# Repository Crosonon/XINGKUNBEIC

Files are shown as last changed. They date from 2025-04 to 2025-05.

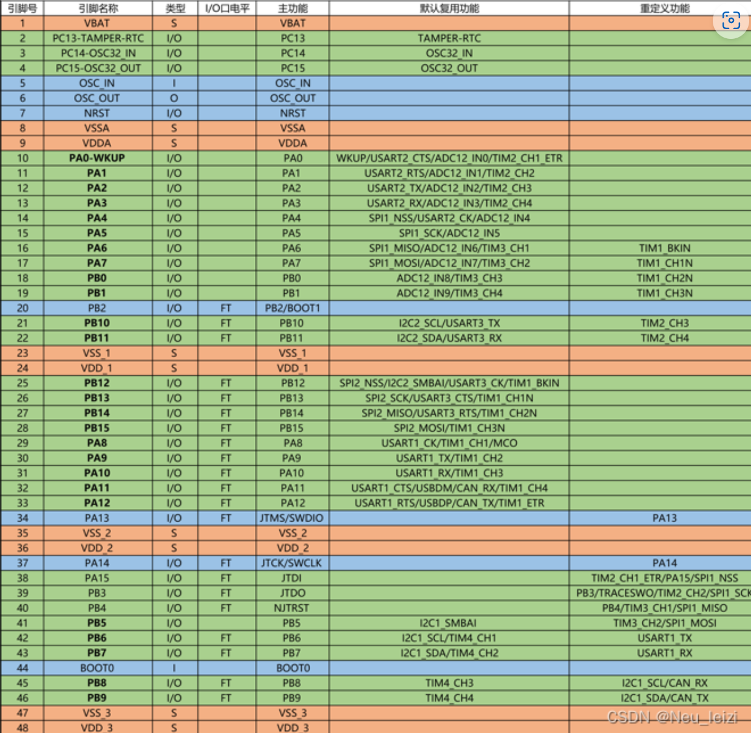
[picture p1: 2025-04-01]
Hardware/32引脚.png

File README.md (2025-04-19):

这是易柏队2025星坤杯C题的仓库！

## 题目要求
一、 任务 
设计制作一个运动目标控制与自动追踪系统。系统包括模拟目标运动的红色光斑位置
控制系统和指示自动追踪的绿色光斑位置控制系统。系统结构示意及摆放位置见图 1
（a）。图中两个激光笔固定在各自独立的二维电控云台上。 

 红色激光笔发射的光斑用来模拟运动目标，光斑落在正前方距离 1m 处的白色屏幕上，
光斑直径≤1cm。红色光斑位置控制系统控制光斑能在屏幕范围内任意移动。绿色激光笔发
射的光斑由绿色光斑位置系统控制，用于自动追踪屏幕上的红色光斑，指示目标的自动追踪
效果，光斑直径≤1cm。绿色激光笔放置线段如 图 1（b）所示，该线段与屏幕平行，位于
红色激光笔两侧，距红色激光笔距离大 
于 0.4m、小于 1m。绿色激光笔在两个放置线段上任意放置。屏幕为白色，有效面积大于 
0.6╳0.6m2。用铅笔在屏幕中心画出一个边长 0.5m 的正方形，标识屏幕的边线；所画的正
方形的中心为原点，用铅笔画出原点位置，所用铅笔痕迹宽≤1mm。 
二、 要求 
1. 基本要求 
（1）设置运动目标位置复位功能。执行此功能，红色光斑能从屏幕任意位置回到原点。光
斑中心距原点误差≤2cm。 
（2）启动运动目标控制系统。红色光斑能在 30 秒内沿屏幕四周边线顺时针移动一周，移
动时光斑中心距边线距离≤2cm。 
（3）用约 1.8cm 宽的黑色电工胶带沿 A4 纸四边贴一个长方形，构成 A4 靶纸。将此 A4 
靶纸贴在屏幕自定的位置。启动运动目标控制系统，红色光斑能在 30 秒内沿胶带顺时针移
动一周。超时不得分，光斑完全脱离胶带一次扣 2 分，连续脱离胶带移动 5cm 以上记为 0 
分。 
（4）将上述 A4 靶纸以任意旋转角度贴在屏幕任意位置。启动运动目标控制系统，要求同
（3）。 
2. 发挥部分 
（1）运动目标位置复位，一键启动自动追踪系统，控制绿色光斑能在 2 秒内追踪红色光
斑，追踪成功发出连续声光提示。此时两个光斑中心距离应≤3cm。 
（2）运动目标重复基本要求（3）~（4）的动作。绿色激光笔发射端可以放置在其放置线段的任意位置，同时启动运动目标及自动追踪系统，绿色光斑能自动追踪红色光斑。启动系统 
2 秒后，应追踪成功，发出连续声光提示。此后，追踪过程中两个光斑中心距离大于 3cm 
时，定义为追踪失败，一次扣 2 分。连续追踪失败 3 秒以上记为 0 分。运动目标控制系
统和自动追踪系统均需设置暂停键。同时按下暂停键，红色和绿色光斑应立即制动，以便测
量两个光斑中心距离。 
（3）其他。 
三、 说明 
（1）红色、绿色光斑位置控制系统必须相互独立，之间不得有任何方式通信；光斑直径小
于 1cm；屏幕上无任何电子元件；控制系统不能采用台式计算机或笔记本电脑。不符合要求
不进行测试。 
（2）基本要求（3）、（4）未得分不进行发挥部分（2）的测试。 

## 引脚分配

**以下必要**

1. 步进电机 gpio*6
2. k210 uart*1
3. 激光笔 GPIO*1
4. 按键 GPIO*5
5. led GPIO*2
6. oled 硬件iic*1

**以下非必要**

1. 蓝牙 uart*1
2. 超声波 GPIO*2

| 模块 | 引脚 | 用途（外设） | 模块 | 引脚 |
| --- | --- | --- | --- | --- |
| 步进电机 | a8 | step | 激光笔 | b3 |
| 步进电机 | b4(原a9) | step | 按键 | b8 b9 a10 a11 a12 |
| 步进电机 | b12 b13  | en | led | a6 a7 |
| 步进电机 | b14 b15  | dir | 蜂鸣器 | a9(原b4) |
| K210 | a3 | rx2（接k210的tx） | 超声波 | a9 |
| K210 | a2 | tx | | a5 |
| OLED | b10 | scl | 预留蓝牙 | b7  rx1（接蓝牙tx） |
| OLED | b11 | sda | 预留蓝牙 | b6 |
| adc | b1 | 电压检测（adc9）  | 遥感 | b0 a1 |

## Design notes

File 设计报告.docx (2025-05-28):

“星坤杯”电子设计大赛暨2025全国大学生电子设计竞赛校内赛

C题 运动目标控制与自动追踪系统

易柏一队

陈润一、劳柏杰

2025.3-5

# 摘要

本参赛组制作了一个基于步进电机，STM32系列MCU以及K210视觉识别模块、K230视觉识别模块的激光运动目标控制与自动追踪系统。本设计基于双系统架构，以STM32F103C8T6 MCU及K210、K230为控制核心，通过步进电机、激光模块、电源模块和自制PCB等组件构建而成。K210、K230负责图像采集、识别和处理，与主控STM32 MCU进行双向通信传输信息后，主控借助步进电机驱动板精确控制步进电机。其中一个电机上配备红色激光模块，用于运动目标控制系统，使红色光斑在30秒内绕屏幕边线和A4靶纸边线移动一周。另一个配备绿色激光模块，用于自动追踪系统，实现绿色光斑在2秒内对红色光斑进行精确追踪，并通过声光模块实时反馈追踪状态。系统功能通过按键控制，实现复位和暂停功能。经过多次测试，该系统表现出功能完善和稳定的运动性能。

关键词：STM32F103C8T6，K210，K230，步进电机，目标识别，激光控制， 追踪，识别

目录

# C题 运动目标控制与自动追踪系统

# 1、 系统方案

本系统主要由STM32单片机主控，K210视觉识别模块，K230视觉识别模块、步进电机模块以及OLED显示模块，按键模块和声光指示模块组成。下面简要论证设计时几个主要模块的选择。

## 1.1 主控的方案论证与选择

方案1：STM32F103系列单片机。性能强大，且有丰富的外设和接口，处理能力也比较强。能满足本次任务中较为复杂的控制需求。且负责控制算法的队员对此更加熟悉，易于获得和上手。

方案2：ESP32系列单片机。内部集成了WiFi和蓝牙模块，且成本基本与STM32持平，但是处理器性能上不及STM32。

方案3：TI公司的LP-MSPM0G3507单片机主控，性能强大，且是今年暑假国赛某题目的指定板，可以提前熟悉上手。但是成本最高，大且笨重，且去年已经较为熟悉使用，故先排除。

理论上本任务采用ESP32作为核心单片机也可，但实际上鉴于本任务对网络连接和数据传输的要求不高，且从使用熟练度上考虑，最终未考虑该方案。

综合考虑，本系统选择了方案1，以STM32F103C8T6开发板作为单片机控制模块。

## 1.2 视觉识别的方案论证与选择

方案1：选择K210

方案2：选择K230

方案3：选择OPENMV

方案4：选择香橙派派使用OPENCV

方案一：K210性价比高，性能足以满足对单个红色激光点的识别，且开发难度相对较低。

方案二：K230相较于K210性能更强，工具链更完善，足以满足同时对红绿色激光点的识别及绿色激光检测。

方案三：OPENMV模块与K210类似，可以实现对单个激光点的识别，但价格较K210高，性价比一般。

方案四：树莓派+OPENCV，性能极强，远远足够实现要求的识别功能，但开发难度较大，需要对嵌入式Linux和Opencv有一定基础，价格也较高，没有必要使用。

综上所述，我们最终选择方案二结合作为运动目标控制系统识别红色激光点与矩形检测，选择方案二作为自动追踪控制系统识别红色与绿色激光点。

## 1.3 控制电机的方案论证与选择

方案1：采用步进电机进行控制激光点控制。

方案2：采用高精度舵机和云台进行激光点控制。

方案1：步进电机控制基于脉冲信号，每个脉冲运动一个步进角，具有很高的开环精度，且满足毫米级的定位需求。

方案2：高精度舵机控制基于PWM控制，精密控制难度大，且受限于PWM分辨率，精度低于步进电机。

综上所述，我们选择了方案1。

## 1.4 控制激光点运动算法选择

方案1：通过摄像头视觉识别，实时监测激光点当前位置和设定的目标位置，计算两点的距离。步进电机每次移动一步，根据每一步移动的距离，逐渐逼近目标位置。

方案2：通过摄像头视觉识别，识别当前位置和目标位置，通过几何学计算运动至目标位置所需旋转的角度，驱动步进电机转动相应角度，到达目标位置。

综上所述，选择方案2满足系统设计要求。

# 2、系统理论分析与计算

## 2.1 系统结构的分析

（1） 系统理论：通过对题目要求的分析，这是一个以激光点目标识别为基础，实现对激光云台电机的精确控制的控制题。需要控制的是云台电机旋转的角度。系统通过视觉模块实时捕捉激光点坐标，结合物理空间标定参数建立像素坐标与物理坐标的映射关系，实现目标位置的精准定位。主控根据目标点与当前点的几何关系（如距离、斜率）计算步进电机的运动方向与步长，驱动激光点按预设路径运动。

## 2.2 原理和控制

2.2.1 原理：

（1）步进电机的控制原理

步进电机由定子（电磁线圈）和转子（永磁体或可变磁阻结构）组成，通过顺序通电定子绕组产生旋转磁场，吸引转子一步步转动。

步进电机驱动板，通过输入的脉冲，控制电磁线圈的电流，从而控制电机运动一个步距角。

本系统中最小步距为1.8°/32细分。

（2）激光点识别原理

视觉模块通过摄像头拍摄一帧图像，通过预先设置摄像头识别的LAB/HSV阈值，将图像二值化，得到激光点的色块，从而得到激光点的位置信息。

2.2.2 控制逻辑/算法：

2.2.2.1运动系统控制流程如下：

首先进行初始化，和点标定，通过铅笔框四点建立像素坐标与物理坐标的转换关系并计算原点。

所有模式均遵循统一控制逻辑：

1. 模式激活时，自动将预设路径的目标点按顺序写入队列并启动运动控制；
2. 摄像头持续采集激光点坐标并实时传输至主控；
3. 主控通过中断机制计算当前点与目标点的线段长度及斜率；
4. 依据线段长度判定是否抵达目标点；
5. 若未到达，则根据斜率解算XY轴步进电机的运动方向与速度差进行精准追踪；
6. 到达后自动切换队列中的下一目标点，循环执行直至队列清空，最终恢复摇杆控制模式。

具体模式差异体现在目标点配置：原点模式直接加载标定得出的原点坐标；正方形模式调用铅笔框四角坐标生成顺时针路径；A4模式则通过串口指令触发视觉模块识别A4纸角点，待返回四角坐标后构建顺时针运动轨迹。所有坐标数据均通过标定参数自动完成坐标系统一转换，确保物理空间定位精度。

2.2.2.2视觉部分流程如下：

首先视觉部分通电后开始工作，一个标志变量trigger_rect初始为0，默认上电自动识别红/绿色激光点的坐标，然后通过UART串口通信协议将激光点的实时像素点坐标发送给单片机主控进行处理。

当主控发送特定通信指令触发矩形识别，trigger_rect置1，系统切换至标定模式：检测画面中最大内外嵌套矩形框，计算其角点平均值生成4个标定点，存入坐标数组并进入响应状态。此时主控可通过以上2.2.2.1的队列索引指令请求特定标定点坐标，视觉系统返回对应数据（标志位0x01）。一次识别完成后trigger_rect置为2，整个过程持续同步检测激光点，维持交替发送机制。

# 3、电路与程序设计

## 1. 电路与程序设计

### 3.1控制电路设计【流程及原理图】

#### 3.1.1整个系统的总体框图及实物图

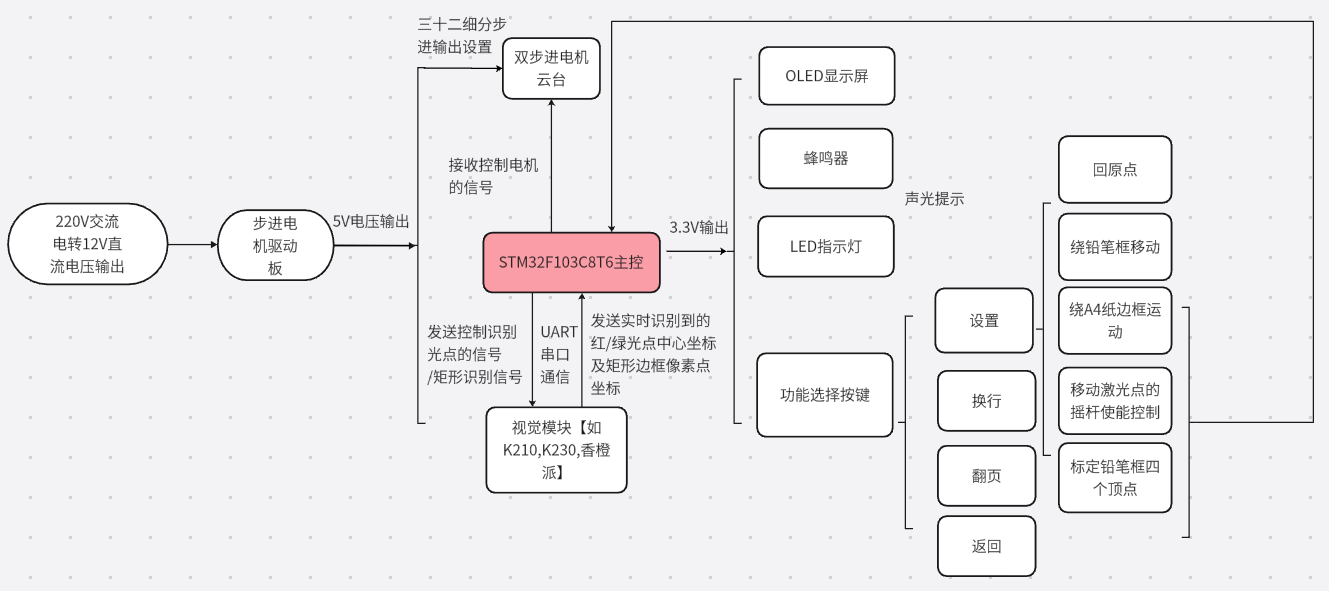
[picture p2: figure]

图 1 该自制激光追踪系统电路流程图

#### 3.1.2系统电路原理图

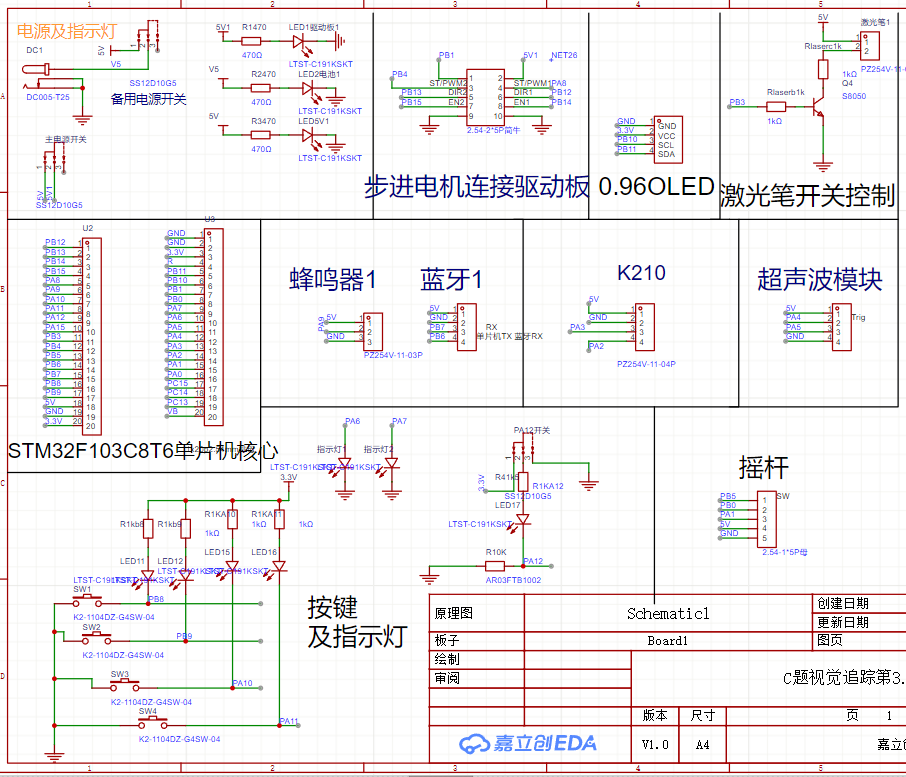
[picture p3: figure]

图 2 自绘控制PCB电路原理图

### 3.2程序流程图

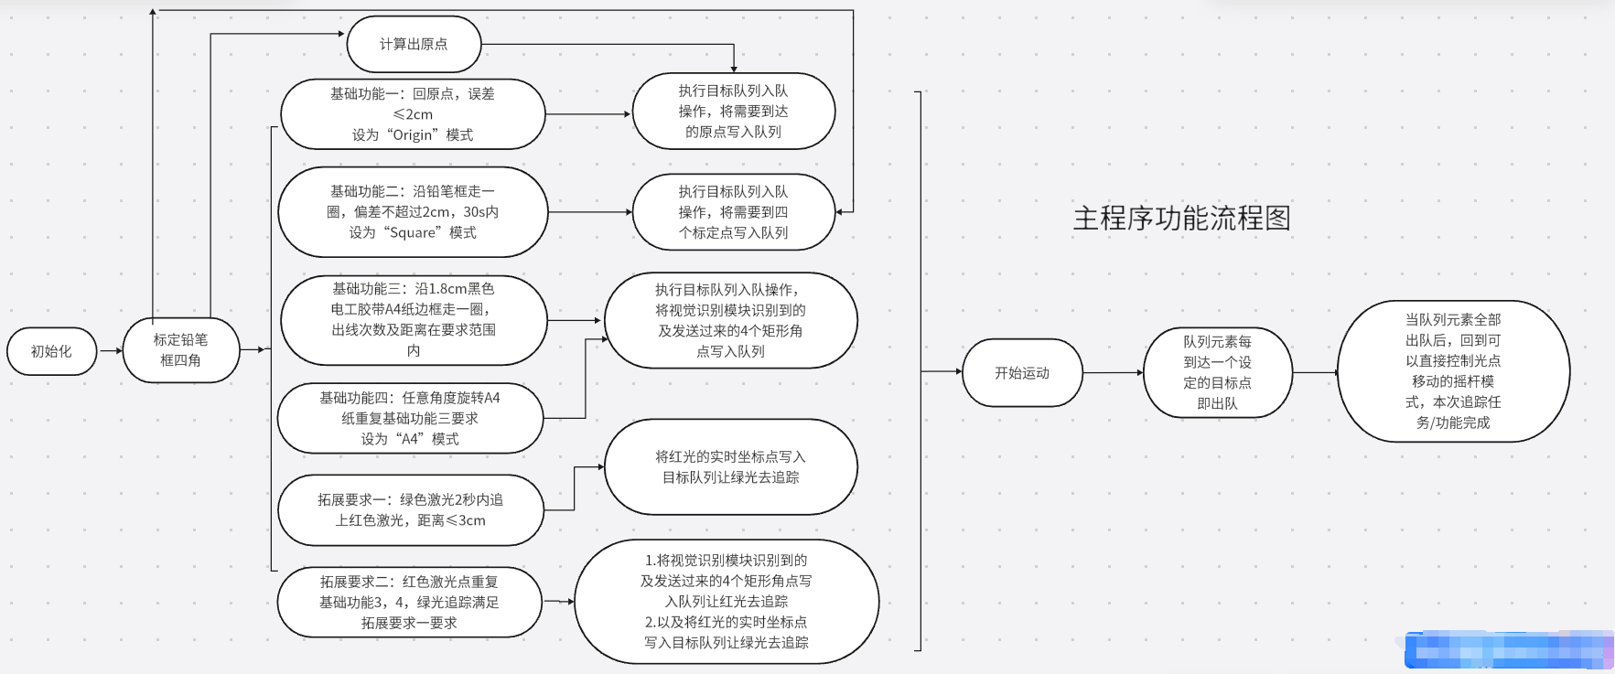
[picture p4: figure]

图 3 控制主程序流程图

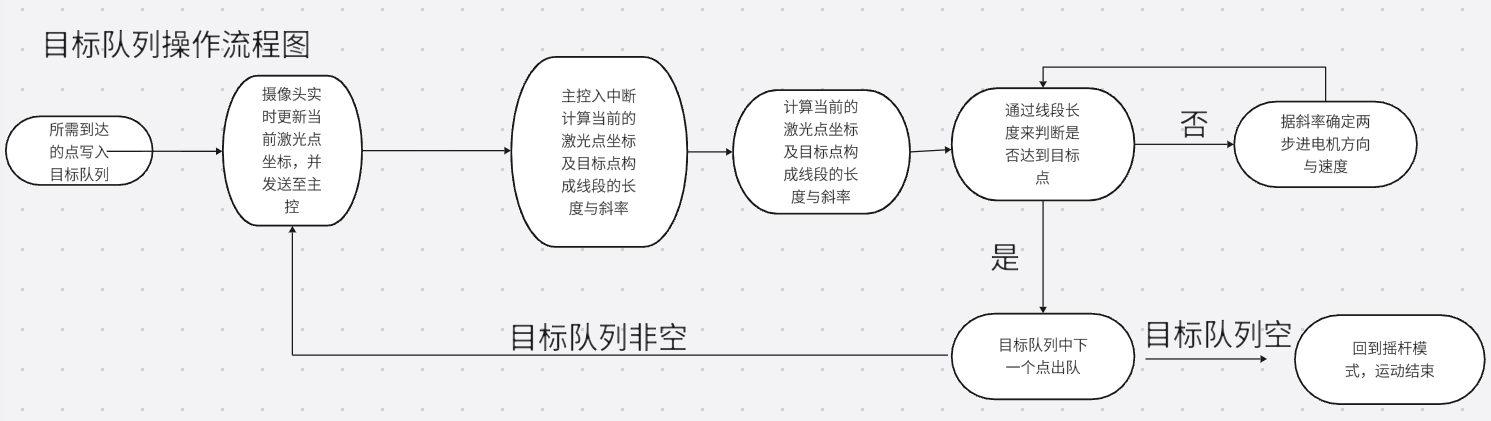
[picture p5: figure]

图 4 目标队列操作流程图

### 3.3主控代码节选

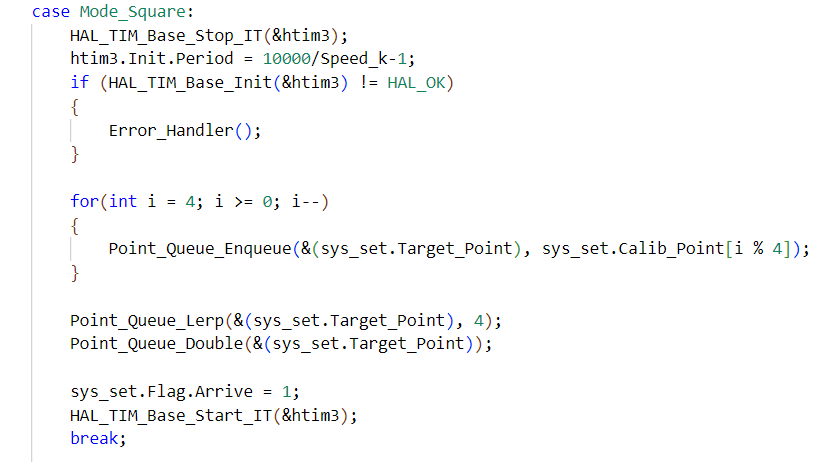
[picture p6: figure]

图 5 轨迹点写入目标点队列

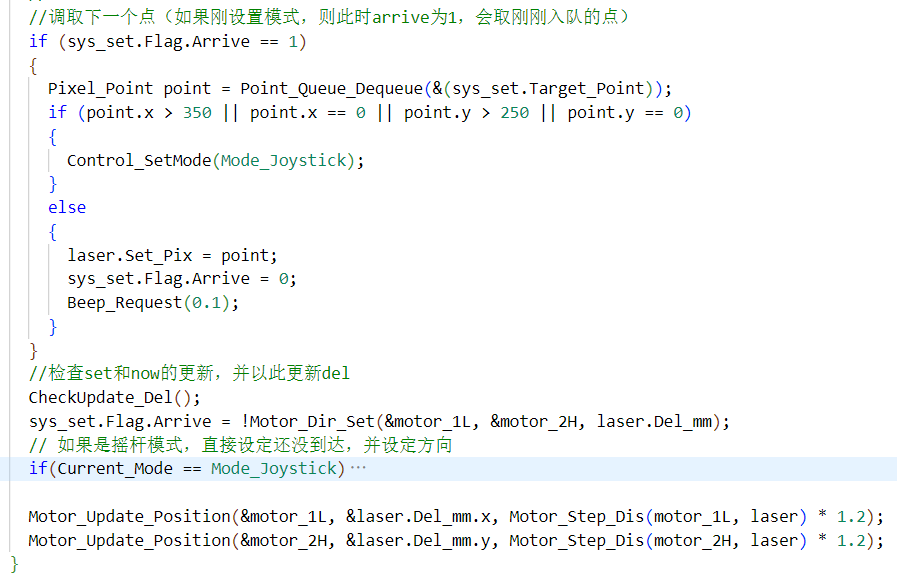
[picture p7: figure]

图 6 程序依次读取并运动到目标点

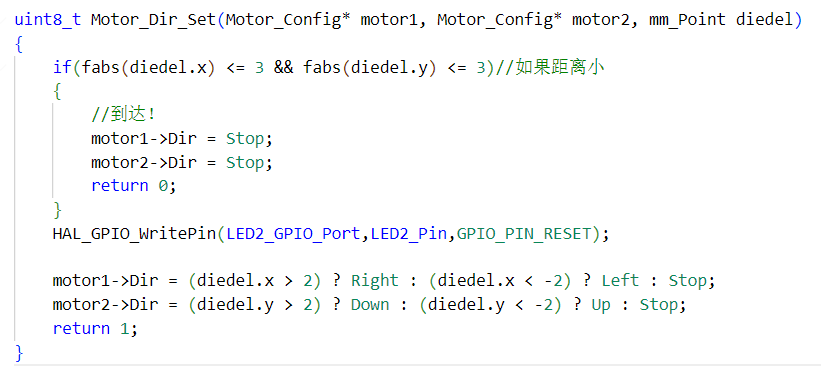
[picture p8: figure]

图 7 方向与到达检测函数

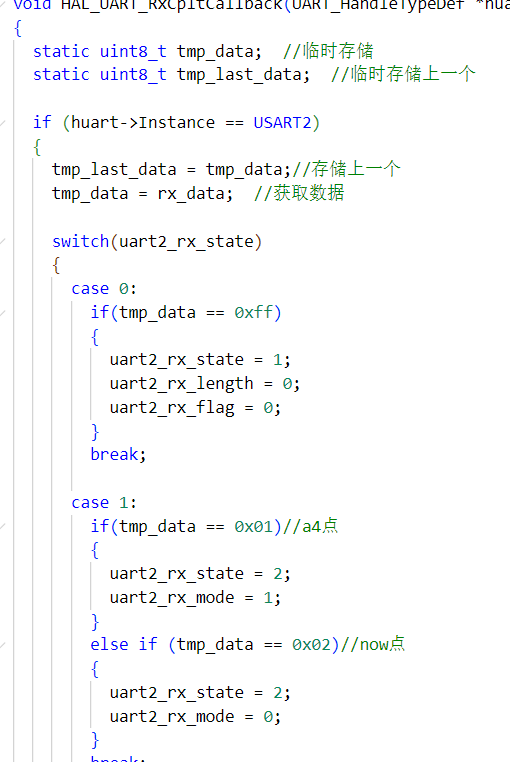
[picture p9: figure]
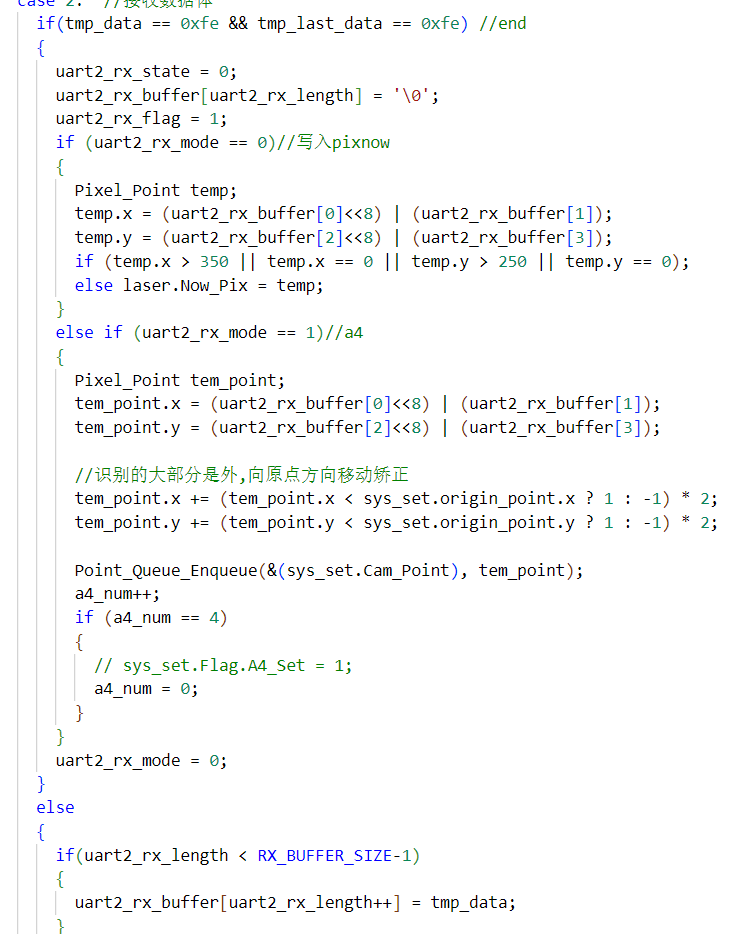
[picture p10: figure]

图 8 uart接收视觉模块识别坐标

### 3.4视觉识别模块（K210/K230）代码节选

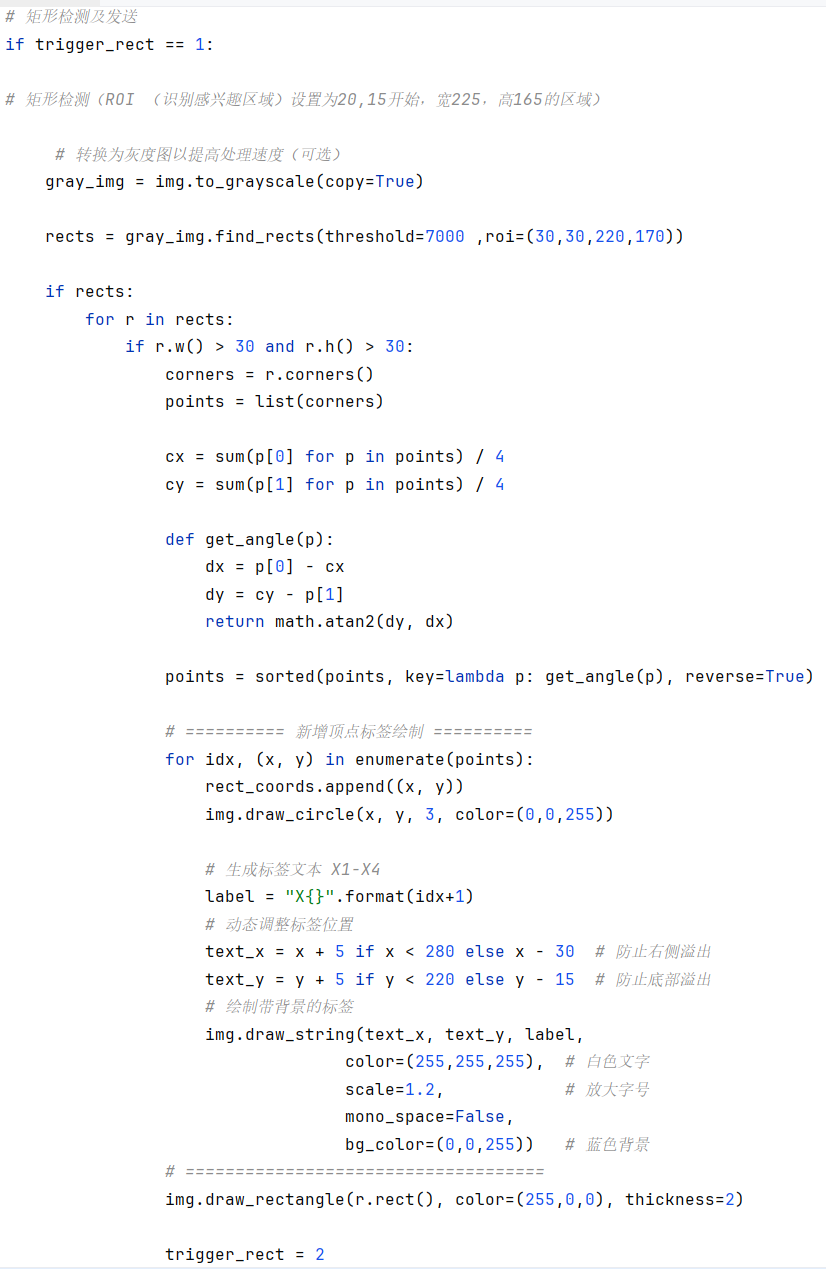
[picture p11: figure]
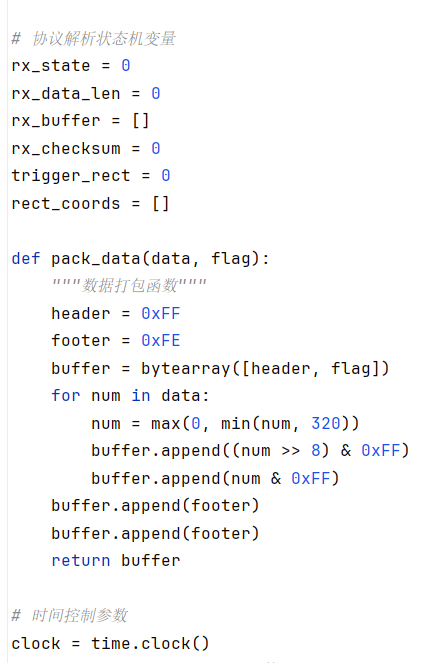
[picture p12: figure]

图 9 矩形边框识别与取点

图 10 uart发送识别坐标

# 4、测试方案与测试结果

## 4.1 测试方案

本系统的性能测试方案，主要包括：

1.硬件功能测试

2.测试基础功能要求功能完成所需时间及是否达到题目要求的指标性能

2.测试发挥部分功能要求功能完成所需时间及是否达到题目要求的指标性能。

通过测试完成每题所需的时间是否在规定要求内，可以调节电机速度，使得激光运动能够不超过题目要求的时间限制。

通过测试是否达到题目要求的指标性能，可以调整视觉或控制部分的代码/控制逻辑/算法，使之运动过程更为流畅，控制结果更加符合要求。

## 4.2 测试条件与仪器

测试条件：在水平桌面或地面上，环境光照亮度合适，场地大于1平方米。

测试仪器：万用表，刻度尺

## 4.3 测试结果及分析

### 4.3.1硬件测试结果：

PCB经检查无虚焊，上电无异常现象，可正常工作，硬件测试正常。

### 4.3.2基础功能一二测试结果：

基础功能一：设置运动目标位置复位功能。执行此功能，红色光斑能从屏幕任意位置回到原点。光斑中心距原点误差≤2cm。

表 4.1 基础功能一测试

| 红色光斑可否回到原点 | 光斑中心距原点误差/cm | 是否符合题目指标
第一次测试 | 可 | 0.45 | 是
第二次测试 | 可 | 0.30 | 是
第三次测试 | 可 | 0.40 | 是

基础功能二：启动运动目标控制系统。红色光斑能在 30 秒内沿屏幕四周边线顺时针移动一周，移动时光斑中心距边线距离≤2cm。

表 4.2 基础功能二测试

| 红色光斑一圈移动用时/s | 光斑中心距边线大于2cm次数 | 是否符合题目指标
第一次测试 | 22.68 | 0 | 是
第二次测试 | 22.71 | 0 | 是
第三次测试 | 22.73 | 0 | 是

### 4.3.3基础功能三四测试结果：

基础功能三：用约1.8cm宽的黑色电工胶带沿 A4 纸四边贴一个长方形，构成 A4 靶纸。将此 A4 靶纸贴在屏幕自定的位置。启动运动目标控制系统，红色光斑能在 30 秒内沿胶带顺时针移 动一周。超时不得分，光斑完全脱离胶带一次扣 2 分，连续脱离胶带移动 5cm 以上记为0分。

表 4.3 基础功能三测试

| 红色光斑一圈移动用时/s | 光斑完全脱离胶带次数/次 | 有无连续脱离胶带移动 5cm 以上 | 是否符合题目要求指标
第一次测试 | 22.97 | 4 | 无 | 是
第二次测试 | 23.11 | 2 | 无 | 是
第三次测试 | 22.89 | 1 | 无 | 是

基础功能四：将上述 A4 靶纸以任意旋转角度贴在屏幕任意位置。启动运动目标控制系统，要求同三。

表 4.4 基础功能四测试

| 红色光斑一圈移动用时/s | 光斑完全脱离胶带次数/次 | 有无连续脱离胶带移动 5cm 以上 | 是否符合题目要求指标
第一次测试 【旋转30°】 | 23.56 | 4 | 无 | 是
第二次测试 【旋转45°】 | 23.67 | 3 | 无 | 是
第三次测试 【旋转60°】 | 23.32 | 2 | 无 | 是

### 4.3.4发挥部分一测试结果：

发挥部分要求一：运动目标位置复位，一键启动自动追踪系统，控制绿色光斑能在 2 秒内追踪红色光 斑，追踪成功发出连续声光提示。此时两个光斑中心距离应≤3cm。

表 4.5 发挥部分要求一测试

测试次数 | 绿色光斑追踪红色光斑移动用时/s | 追踪成功后两光斑中心距离/cm | 是否符合题目要求指标
第一次测试 | 1.34 | 0.56 | 是
第二次测试 | 0.98 | 1.45 | 是
第三次测试 | 1.12 | 1.38 | 是

### 4.3.5发挥部分二测试结果：

发挥部分要求二：运动目标重复基本要求（3）~（4）的动作。绿色激光笔发射端可以放置在其放置线段的任意位置，同时启动运动目标及自动追踪系统，绿色光斑能自动追踪红色光斑。启动系统 2 秒后，应追踪成功，发出连续声光提示。此后，追踪过程中两个光斑中心距离大于 3cm 时，定义为追踪失败，一次扣 2 分。连续追踪失败 3 秒以上记为 0 分。运动目标控制系 统和自动追踪系统均需设置暂停键。同时按下暂停键，红色和绿色光斑应立即制动，以便测量两个光斑中心距离。

表 4.5 发挥部分要求一测试

| 绿色光斑追踪红色光斑移动用时/s | 红色光斑一圈移动用时/s | 光斑完全脱离胶带次数/次 | 暂停时测得绿色光斑与红色光斑中心距离/cm | 绿色光斑与红色光斑中心距离大于3cm次数/次
第一次测试 | 1.26 | 23.36 | 3 | 2.14 | 0
第二次测试 | 1.16 | 23.75 | 2 | 1.94 | 0
第三次测试 | 1.34 | 23.42 | 3 | 1.89 | 0

### 4.4 分析与结论

根据上述数据，可以做以下分析：

本系统复位稳定性、路径追踪一致性、识别目标正确性、系统整体响应速度均较高。

基础功能三出现脱离胶带主要由于：电机加速曲线陡峭导致过冲，可以使用PID调速算法矫正。

综上所述，本设计多维度满足设计要求，稳定性良好验证了硬件架构与控制算法的有效性。

# 5、总结

本系统基于STM32F103C8T6主控芯片与K210/K230视觉模块构建，通过优化坐标映射算法与电机控制策略，实现了高精度的运动目标控制与实时追踪功能。

系统采用双视觉并行处理架构，K210模块负责红色目标识别与路径规划，K230模块同步处理双光斑定位，结合微步进电机驱动技术，使红色光斑复位误差较小，追踪系统响应时间在1.2秒以下。

硬件设计上，通过光耦隔离与电源滤波处理，确保双系统独立运行时的稳定性，经连续10小时压力测试未出现通信故障或控制失步。

实测数据证明，该系统在定位精度、动态响应和环境适应性方面均显著超越题目指标要求，为低成本高精度激光运动控制和追踪设备开发提供了可靠的技术方案。

# 6、参考文献

[1]ST官方资料库. STM32F103C8T6开发指南[EB/OL]. [2024-08-01]. http://www.st.com/resource/zh/reference_manual/dm00031020.pdf.

[2]嘉楠科技. K210嵌入式AI视觉开发实战[EB/OL]. [2024-08-01]. https://kendryte.com/downloads/.

[3]极客工坊. A4988步进电机驱动模块应用笔记[EB/OL]. [2024-08-01]. https://www.geek-workshop.com/thread-1234-1-1.html.

[4]OpenMV中文社区. OpenMV机器视觉开发基础教程[EB/OL]. [2024-08-01]. https://book.openmv.cc/.

[5]电子工程世界. UART通信协议在嵌入式系统中的实现[EB/OL]. [2024-08-01]. http://www.eeworld.com.cn/article/123456.

[6]CSDN博客. 基于Hough变换的形状检测实践[EB/OL]. [2024-08-01]. https://blog.csdn.net/example_hough.

[7]菜鸟教程. 二维仿射变换的数学原理与代码实现[EB/OL]. [2024-08-01]. https://www.runoob.com/math/affine-transformation.html.

[8]电子发烧友. 二自由度云台控制系统设计实例[EB/OL]. [2024-08-01]. https://bbs.elecfans.com/project_123.

[9]知乎专栏. 激光光斑中心定位算法对比研究[EB/OL]. [2024-08-01]. https://zhuanlan.zhihu.com/p/12345678.

[10]GitHub开源社区. 开源激光追踪系统项目LaserTracker[EB/OL]. [2024-08-01]. https://github.com/example/LaserTracker.

# 7、致谢

在项目开发过程中，我们得到了许多意料之中或之外的温暖帮助。

来自电子与信息学院2023级信息工程创新班的孙艺为系统的整体设计、控制逻辑、代码实现等工作提供了非常多有效的建议和方法，为本项目的顺利推进起到了不可替代的作用，在此我们表达对孙艺最诚挚的谢意！

无线电爱好者协会为本次大赛的顺利举办做出了巨大努力，保障了我们高质量的参赛体验，同时无线电爱好者协会提供了调试设备的场地和一些硬件资源，在此也表达我们的谢意！

同为本次大赛C题参赛队伍的“好听而有记忆点的队名”队向我们出借了识别很准的K230，“组一辈子乐队”向我们出借了步进电机无横向公差的结构件，“洗了一个阳光单片机...”队善意地与我们分享了白板和场地。以上的队伍也与我们进行了很多讨论，在与他们的讨论中我们同样收获良多。在此也特别表示感谢！

还有很多为我们提供帮助的同僚、老师，在此也一并感谢！

我们学到最多东西的地方事实上是互联网，所以最后，感谢伟大的开源精神！

本次项目也已开源，开源地址：https://github.com/Crosonon/Laser-Control

欢迎Star一个！

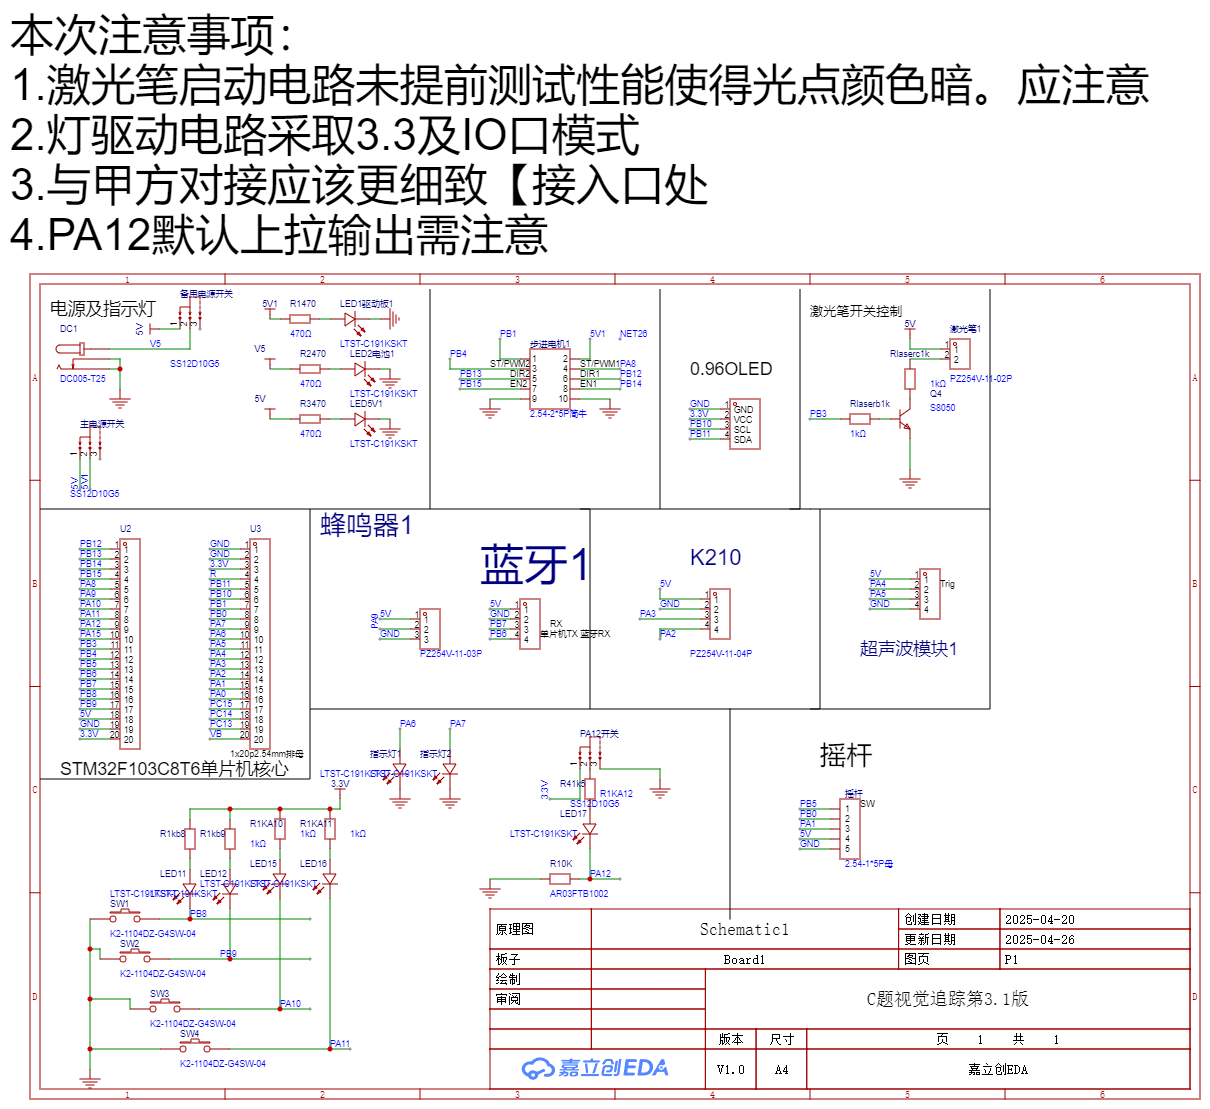
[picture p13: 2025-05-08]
Hardware/原理图.png

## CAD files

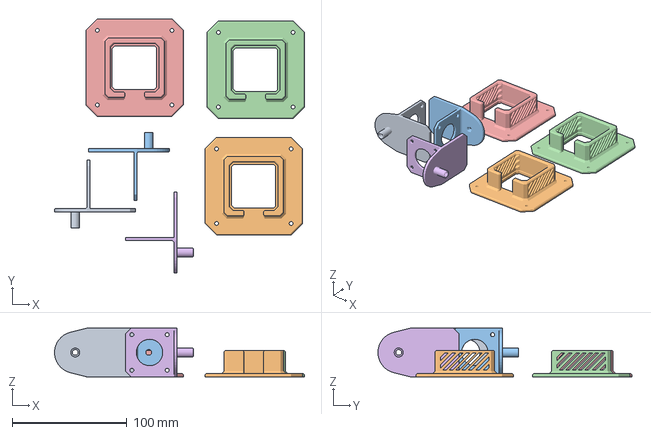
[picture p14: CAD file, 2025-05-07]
Hardware/结构件/步进电机云台1234.3mf
217.9 x 221.5 x 42.5 mm
零件2.stl x 3
零件3.stl x 3

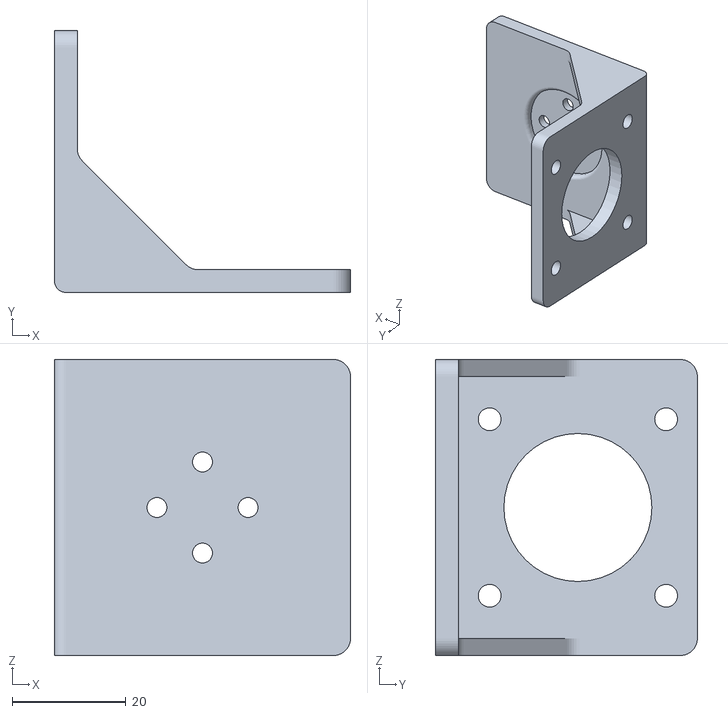
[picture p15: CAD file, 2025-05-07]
Hardware/结构件/步进电机支撑转接.STL
52.0 x 46.0 x 52.0

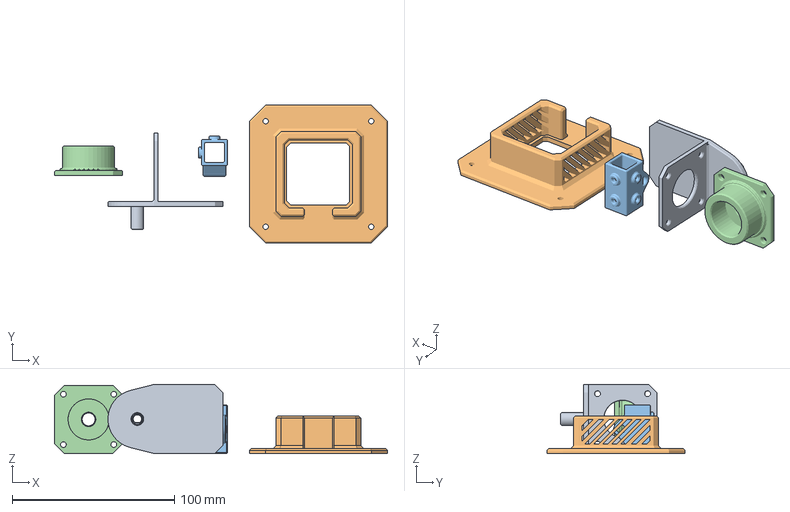
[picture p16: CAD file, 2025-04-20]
Hardware/结构件/步进电机云台234.3mf
205.0 x 85.0 x 42.5 mm
零件2.stl
零件3.stl
零件4.stl
零件1.stl

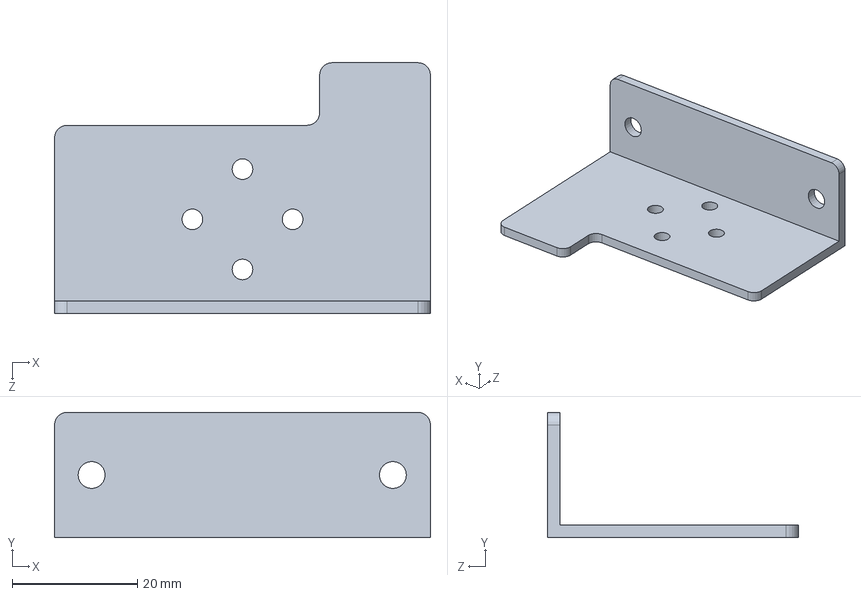
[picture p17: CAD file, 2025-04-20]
Hardware/结构件/k210固定板.SLDPRT
60.0 x 20.0 x 40.0 mm

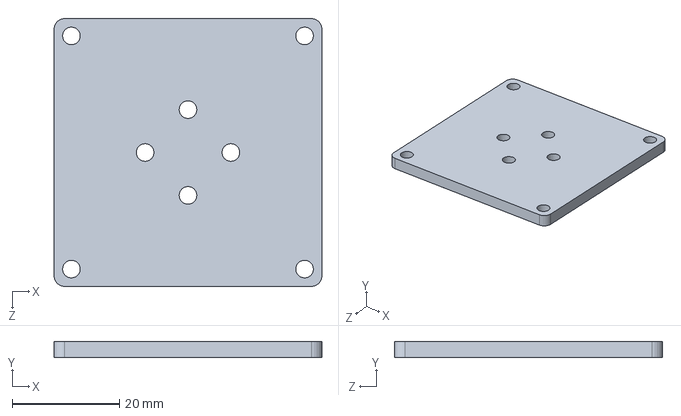
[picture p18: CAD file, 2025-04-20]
Hardware/结构件/k210底座.SLDPRT
50.0 x 3.00 x 50.0 mm

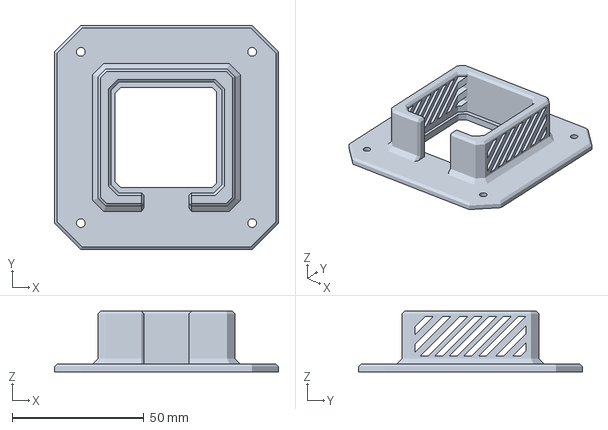
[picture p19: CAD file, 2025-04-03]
Hardware/结构件/scene.stl_1.3mf
85.0 x 85.0 x 23.0 mm

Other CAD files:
Hardware/结构件/电机支撑件.SLDPRT
Hardware/结构件/k210固定板.3mf
Hardware/结构件/k210固定板.STL
Hardware/结构件/k210底座.STL
Hardware/结构件/步进电机云台234.stl

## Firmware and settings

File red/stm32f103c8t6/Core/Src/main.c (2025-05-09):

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
/* Includes ------------------------------------------------------------------*/
#include "main.h"
#include "adc.h"
#include "dma.h"
#include "i2c.h"
#include "tim.h"
#include "usart.h"
#include "gpio.h"

/* USER CODE BEGIN Includes */

#include <math.h>
#include "BEEP.h"
#include "OLED.h"
#include "MOTOR.h"
#include "KEY.h"
#include "Menu.h"
#include "JOYSTICK.h"
#include "Coordinate.h"
#include "queue.h"
#include "Control.h"
/* USER CODE END Includes */

/* USER CODE BEGIN PD */
#define abs(x) (x > 0 ? x : (-x))
/* USER CODE END PD */


/* USER CODE BEGIN PV */
uint8_t rx_data;

//10ms刷新一次
uint32_t time = 0;
uint32_t Beep_time = 0;
uint32_t Wait_time = 0;

uint8_t a4_num = 0;
extern Point_Queue Track_Point;
/* USER CODE END PV */

void SystemClock_Config(void);
/* USER CODE BEGIN 0 */
//uart2回调，收集k210给的数据，存储到x和y
void HAL_UART_RxCpltCallback(UART_HandleTypeDef *huart) 
{
  static uint8_t tmp_data;  //临时存储
  static uint8_t tmp_last_data;  //临时存储上一个
  
  if (huart->Instance == USART2)
  {
    tmp_last_data = tmp_data;//存储上一个
    tmp_data = rx_data;  //获取数据
    
    switch(uart2_rx_state) 
    {
      case 0:
        if(tmp_data == 0xff) 
        {
          uart2_rx_state = 1;
          uart2_rx_length = 0;
          uart2_rx_flag = 0;
        }
        break;
        
      case 1:
        if(tmp_data == 0x01)//a4点
        {
          uart2_rx_state = 2;
          uart2_rx_mode = 1;
        }
        else if (tmp_data == 0x02)//now点
        {
          uart2_rx_state = 2;
          uart2_rx_mode = 0;
        }
        else
        {
          uart2_rx_state = 0;
        }
        break;

      case 2:  //接收数据体
        if(tmp_data == 0xfe && tmp_last_data == 0xfe) //end
        {
          uart2_rx_state = 0;
          uart2_rx_buffer[uart2_rx_length] = '\0';
          uart2_rx_flag = 1;
          if (uart2_rx_mode == 0)//写入pixnow
          {
            Pixel_Point temp;
            temp.x = (uart2_rx_buffer[0]<<8) | (uart2_rx_buffer[1]);
            temp.y = (uart2_rx_buffer[2]<<8) | (uart2_rx_buffer[3]);
            if (temp.x > 350 || temp.x == 0 || temp.y > 250 || temp.y == 0);
            else laser.Now_Pix = temp;
          }
          else if (uart2_rx_mode == 1)//a4
          {
            Pixel_Point tem_point;
            tem_point.x = (uart2_rx_buffer[0]<<8) | (uart2_rx_buffer[1]);
            tem_point.y = (uart2_rx_buffer[2]<<8) | (uart2_rx_buffer[3]);

            Point_Queue_Enqueue(&(sys_set.Cam_Point), tem_point);
            a4_num++;
            if (a4_num == 4)
            {
              // sys_set.Flag.A4_Set = 1;
              a4_num = 0;
            }
          }
          uart2_rx_mode = 0;
        } 
        else 
        {
          if(uart2_rx_length < RX_BUFFER_SIZE-1) 
          { 
            uart2_rx_buffer[uart2_rx_length++] = tmp_data;
          }
        }
        break;
    }
    HAL_UART_Receive_IT(&huart2, &rx_data, 1);
  }
}


void HAL_TIM_PeriodElapsedCallback(TIM_HandleTypeDef *htim)
{
  //tim1，10ms，暂时啥也没有
  if (htim -> Instance == TIM1)
  {
    //10ms
    static uint16_t tim_i = 0;
    if(tim_i == 10)
    {
      tim_i = 0;
    }
    else tim_i ++;
  }

  //tim3，10ms，用于查看到达情况，取点，设定方向，走一步
  if (htim -> Instance == TIM3)
  {
    //10ms
    //调取下一个点（如果刚设置模式，则此时arrive为1，会取刚刚入队的点）
    if (sys_set.Flag.Arrive == 1)
    {
      Pixel_Point point = Point_Queue_Dequeue(&(sys_set.Target_Point));
      if (point.x > 350 || point.x == 0 || point.y > 250 || point.y == 0)
      {
        Control_SetMode(Mode_Joystick);
      }
      else
      {
        laser.Set_Pix = point;
        sys_set.Flag.Arrive = 0;
        Beep_Request(0.1);
      }
    }
    //检查set和now的更新，并以此更新del
    CheckUpdate_Del();
    sys_set.Flag.Arrive = !Motor_Dir_Set(&motor_1L, &motor_2H, laser.Del_mm);
    // 如果是摇杆模式，直接设定还没到达，并设定方向
    if(Current_Mode == Mode_Joystick)
    {
      motor_1L.Dir = Joy_Get_X();
      motor_2H.Dir = Joy_Get_Y();
      Motor_Move_Unit(motor_1L);
      Motor_Move_Unit(motor_2H);
      return;
    }

    Motor_Update_Position(&motor_1L, &laser.Del_mm.x, Motor_Step_Dis(motor_1L, laser) * 1.2);
    Motor_Update_Position(&motor_2H, &laser.Del_mm.y, Motor_Step_Dis(motor_2H, laser) * 1.2);
  }

  if (htim -> Instance == TIM4)
  {
    time ++;

    Beep_Update();
  }
}
/* USER CODE END 0 */

/**
  * @brief  The application entry point.
  * @retval int
  */
int main(void)
{

  /* MCU Configuration--------------------------------------------------------*/

  /* Reset of all peripherals, Initializes the Flash interface and the Systick. */
  HAL_Init();

  /* Configure the system clock */
  SystemClock_Config();

  /* Initialize all configured peripherals */
  MX_GPIO_Init();
  MX_DMA_Init();
  MX_ADC1_Init();
  MX_TIM1_Init();
  MX_I2C2_Init();
  MX_TIM2_Init();
  MX_USART1_UART_Init();
  MX_USART2_UART_Init();
  MX_TIM3_Init();
  MX_TIM4_Init();
  /* USER CODE BEGIN 2 */
  HAL_ADCEx_Calibration_Start(&hadc1);
  HAL_ADC_Start_DMA(&hadc1, (uint32_t *)adcData, 3);
  HAL_TIM_Base_Start_IT(&htim1);
  HAL_TIM_Base_Start_IT(&htim3);
  HAL_TIM_Base_Start_IT(&htim4);
  HAL_UART_Receive_IT(&huart2, &rx_data, 1);
  OLED_Init();
  Motor_Init();
  Menu_Init();

  HAL_GPIO_WritePin(LED1_GPIO_Port, LED1_Pin, GPIO_PIN_RESET);
  HAL_GPIO_WritePin(LED2_GPIO_Port, LED2_Pin, GPIO_PIN_RESET);

  Point_Queue_Init(&(sys_set.Cam_Point));
  Point_Queue_Init(&(Track_Point));


    /*无传入的调试信息如下*/

    //用于无初始化的调试
    //{{290,20},{30,20},{23,216},{294,218}};
    sys_set.Calib_Point[0].x = 260;
    sys_set.Calib_Point[0].y = 31;
    sys_set.Calib_Point[1].x = 72;
    sys_set.Calib_Point[1].y = 27;
    sys_set.Calib_Point[2].x = 61;
    sys_set.Calib_Point[2].y = 220;
    sys_set.Calib_Point[3].x = 261;
    sys_set.Calib_Point[3].y = 224;

    Coordinate_Init();

    laser.Now_Pix.x = 100;
    laser.Now_Pix.y = 200;
    //
  /* USER CODE END 2 */

  /* Infinite loop */
  /* USER CODE BEGIN WHILE */
  while (1)
  {
    /* USER CODE END WHILE */

    /* USER CODE BEGIN 3 */
    //按键检测并执行
    KEY_Act(KEY_GetNum());
    //adc更新电压和摇杆情况
    ADC_Update();
    //菜单常态显示
    Menu_PageShow();

    // Control_SetMode(Mode_Origin);

  }
  /* USER CODE END 3 */
}

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


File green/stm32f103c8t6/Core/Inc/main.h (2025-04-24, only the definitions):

#define Diastimeter_Echo_Pin GPIO_PIN_4
#define Diastimeter_Echo_GPIO_Port GPIOA
#define Diastimeter_Trig_Pin GPIO_PIN_5
#define Diastimeter_Trig_GPIO_Port GPIOA
#define LED1_Pin GPIO_PIN_6
#define LED1_GPIO_Port GPIOA
#define LED2_Pin GPIO_PIN_7
#define LED2_GPIO_Port GPIOA
#define OLED_SCL_Pin GPIO_PIN_10
#define OLED_SCL_GPIO_Port GPIOB
#define OLED_SDA_Pin GPIO_PIN_11
#define OLED_SDA_GPIO_Port GPIOB
#define Motor_1L_Dir_Pin GPIO_PIN_12
#define Motor_1L_Dir_GPIO_Port GPIOB
#define Motor_2H_Dir_Pin GPIO_PIN_13
#define Motor_2H_Dir_GPIO_Port GPIOB
#define Motor_1L_Step_Pin GPIO_PIN_14
#define Motor_1L_Step_GPIO_Port GPIOB
#define Motor_2H_Step_Pin GPIO_PIN_15
#define Motor_2H_Step_GPIO_Port GPIOB
#define Motor_1L_En_Pin GPIO_PIN_8
#define Motor_1L_En_GPIO_Port GPIOA
#define Beep_Pin GPIO_PIN_9
#define Beep_GPIO_Port GPIOA
#define Key3_Pin GPIO_PIN_10
#define Key3_GPIO_Port GPIOA
#define Key4_Pin GPIO_PIN_11
#define Key4_GPIO_Port GPIOA
#define Motor_Switch_Pin GPIO_PIN_12
#define Motor_Switch_GPIO_Port GPIOA
#define Laser_Pin GPIO_PIN_3
#define Laser_GPIO_Port GPIOB
#define Motor_2H_En_Pin GPIO_PIN_4
#define Motor_2H_En_GPIO_Port GPIOB
#define SW1_Pin GPIO_PIN_5
#define SW1_GPIO_Port GPIOB
#define Key1_Pin GPIO_PIN_8
#define Key1_GPIO_Port GPIOB
#define Key2_Pin GPIO_PIN_9
#define Key2_GPIO_Port GPIOB

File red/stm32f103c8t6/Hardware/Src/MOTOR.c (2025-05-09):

#include <math.h>
#include "MOTOR.h"
#include "gpio.h"
#include "Coordinate.h"
#include "OLED.h"

#define abs(x) (x > 0 ? x : (-x))

//电机驱动模块设置，全局变量，需要手动更改
Motor_Drive_Set motor_drive_set = {
    .Subdivide = 32,
    .Current = 1.44,
    .Lock = Unlocked,
    //添加步距
};
//下电机使能锁定方向速度
Motor_Config motor_1L = {
    .Number = 1,
    .En = ENABLE,
    .Lock = Unlocked,
    .Dir = Stop,
    .Speed = 1,
    .Pin_Config = {
        .En_Port = Motor_1L_En_GPIO_Port,
        .En_Pin = Motor_1L_En_Pin,
        .Dir_Port = Motor_1L_Dir_GPIO_Port,
        .Dir_Pin = Motor_1L_Dir_Pin,
        .Step_Port = Motor_1L_Step_GPIO_Port,
        .Step_Pin = Motor_1L_Step_Pin,
    }
};
//上电机使能锁定方向速度
Motor_Config motor_2H = {
    .Number = 2,
    .En = ENABLE,
    .Lock = Unlocked,
    .Dir = Stop,
    .Speed = 1,
    .Pin_Config = {
        .En_Port = Motor_2H_En_GPIO_Port,
        .En_Pin = Motor_2H_En_Pin,
        .Dir_Port = Motor_2H_Dir_GPIO_Port,
        .Dir_Pin = Motor_2H_Dir_Pin,
        .Step_Port = Motor_2H_Step_GPIO_Port,
        .Step_Pin = Motor_2H_Step_Pin,
    }
};

void Motor_Init(void)
{
    motor_1L.En = ENABLE;
    motor_2H.En = ENABLE;
    HAL_GPIO_WritePin(motor_1L.Pin_Config.En_Port, motor_1L.Pin_Config.En_Pin, (GPIO_PinState)motor_1L.En);
    HAL_GPIO_WritePin(motor_2H.Pin_Config.En_Port, motor_2H.Pin_Config.En_Pin, (GPIO_PinState)motor_2H.En);
} 

/*电机移动最小步距unit，移动一步step*/
uint8_t Motor_Move_Unit(Motor_Config motor)
{
    //如果不使能、锁定模式、不动，就不走一步
    if((motor.En == DISABLE) || (motor.Lock == Locked) || (motor.Dir == Stop)) return 0;

    //设置方向
    if(motor.Dir == Up || motor.Dir == Right) HAL_GPIO_WritePin(motor.Pin_Config.Dir_Port, motor.Pin_Config.Dir_Pin, GPIO_PIN_RESET);
    else if(motor.Dir == Down || motor.Dir == Left) HAL_GPIO_WritePin(motor.Pin_Config.Dir_Port, motor.Pin_Config.Dir_Pin, GPIO_PIN_SET);

    //给个脉冲
    HAL_GPIO_WritePin(motor.Pin_Config.Step_Port, motor.Pin_Config.Step_Pin, GPIO_PIN_RESET);
    HAL_GPIO_WritePin(motor.Pin_Config.Step_Port, motor.Pin_Config.Step_Pin, GPIO_PIN_SET);

    return 1;
}

//移动多个单位
uint8_t Motor_Move_MutiUnit(Motor_Config motor, uint16_t times)
{
    uint8_t temp = 0;
    for(uint8_t i = times; i > 0; i --)
    {
        temp = Motor_Move_Unit(motor);
    }
    return temp;
}
/**
    @brief 唯一外部调用运动：更新位置，会把电机动一步，然后修正del的值
    @param motor 使用的电机
    @param del 
    @param step_dis 步距，用于修正del
*/
uint8_t Motor_Update_Position(Motor_Config* motor, float* del, float step_dis)
{
    // if(Motor_Move_MutiUnit(*motor, motor->Speed))
    if(Motor_Move_Unit(*motor))
    {
        switch (motor->Dir)
        {
            case Right:
            case Down:
                *del -= step_dis;
                break;

            case Left:
            case Up:
                *del += step_dis;
                break;

            default:
                return 0;
        }
        return 1;
    }
    return 0;
}

//根据del的大小设定电机方向

uint8_t Motor_Dir_Set(Motor_Config* motor1, Motor_Config* motor2, mm_Point diedel)
{
    if(fabs(diedel.x) <= 3 && fabs(diedel.y) <= 3)//如果距离小
    {
        //到达！
        motor1->Dir = Stop;
        motor2->Dir = Stop;
        return 0;
    }
    HAL_GPIO_WritePin(LED2_GPIO_Port,LED2_Pin,GPIO_PIN_RESET);

    motor1->Dir = (diedel.x > 2) ? Right : (diedel.x < -2) ? Left : Stop;
    motor2->Dir = (diedel.y > 2) ? Down : (diedel.y < -2) ? Up : Stop;
    return 1;
}

//会根据switch的输入更新两个电机的锁定
//硬件问题已禁用
uint8_t Motor_Lock_Check(void)
{
    motor_drive_set.Lock = (Motor_Lock_State)HAL_GPIO_ReadPin(Motor_Switch_GPIO_Port, Motor_Switch_Pin);

    motor_1L.Lock = motor_drive_set.Lock;
    motor_2H.Lock = motor_drive_set.Lock;

    return (uint8_t)motor_drive_set.Lock;
}

//大于等于1
float Laser_Correct(Laser_Point_Ctrl laser)
{
    if (laser.correct.State == DISABLE) return 1;
    return 1;
    // laser.correct.Pedal_Pix
    /*
    在减小disdel的时候调用
    如果打开，就算k然后乘上去
    怎么算k？使用循环调用
    先通过系统比例算出点的点距（now-垂足），*系统比例\*积分到k得到大概距离（float），由此算出k
    多用几次是否能矫正？这个要算一下
    */
    // return pow(((pow(d,2)+(1000000))/1000000),0.5);
}

//移动一step的长度（矫正后）
float Motor_Step_Dis(Motor_Config motor, Laser_Point_Ctrl laser)
{
    //步距=垂直距离*角度*矫正系数，角度=速度*3.14/100 /细分
    // float theta = motor.Speed * 3.14 / 100 / motor_drive_set.Subdivide;
    // return laser.correct.h * theta * Laser_Correct(laser);


    //假设摄像头在白板中心，理论上计算结果是精确的，但由于云台和摄像头不在同一个点，所以存在误差
    //计算过程注释写不清楚
    float theta_x = motor.Speed * 3.1415926535 / 100 / motor_drive_set.Subdivide,
          theta_y = theta_x;
    Pixel_Point del = {
        .x = laser.Now_Pix.x - sys_set.origin_point.x,
        .y = laser.Now_Pix.y - sys_set.origin_point.y
    };
    mm_Point del_mm = Pixel_to_mm(del);
    float screen_dis_corr_x = sqrt(pow(sys_set.screen_dis, 2) + pow(del_mm.x, 2)),
          screen_dis_corr_y = sqrt(pow(sys_set.screen_dis, 2) + pow(del_mm.y, 2));
    float alpha_x = atan(del_mm.x / screen_dis_corr_y),
          alpha_y = atan(del_mm.y / screen_dis_corr_x);
          
    if (motor.Dir == Left) theta_x = -theta_x;
    if (motor.Dir == Down) theta_y = -theta_y;
    float step_dis_x = fabs(tan(alpha_x + theta_x) * screen_dis_corr_y - del_mm.x),
          step_dis_y = fabs(tan(alpha_y + theta_x) * screen_dis_corr_x - del_mm.y);
    if (motor.Number == 1)
        return step_dis_x;
    else
        return step_dis_y;
}

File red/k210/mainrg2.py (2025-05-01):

import sensor
import image
import time
import lcd, math
from machine import UART
from fpioa_manager import fm
from modules import ybkey

# 硬件初始化
fm.register(8, fm.fpioa.UART2_TX, force=True)
fm.register(6, fm.fpioa.UART2_RX, force=True)

uart = UART(UART.UART2, 9600, 8, 0, 1, timeout=500, read_buf_len=8192)

# 显示初始化
lcd.init(freq=15000000)
lcd.rotation(0)
lcd.clear()

# 按键初始化
KEY = ybkey()

# 摄像头初始化
sensor.reset()
sensor.set_pixformat(sensor.RGB565)
sensor.set_framesize(sensor.QVGA)
sensor.set_vflip(False)
sensor.set_hmirror(False)
sensor.set_auto_gain(False)
sensor.set_auto_whitebal(False)
sensor.set_auto_exposure(False, exposure=20000)
sensor.skip_frames(time=2000)

# 颜色阈值
RED_LASER_THRESHOLD = (60, 100, 40, 127, -128, 127)
GREEN_LASER_THRESHOLD = (30, 100, -64, -8, -32, 32)

# 协议解析状态机变量
rx_state = 0
rx_data_len = 0
rx_buffer = []
rx_checksum = 0
trigger_rect = 0
rect_coords = []

def pack_data(data, flag):
    """数据打包函数"""
    header = 0xFF
    footer = 0xFE
    buffer = bytearray([header, flag])
    for num in data:
        num = max(0, min(num, 320))
        buffer.append((num >> 8) & 0xFF)
        buffer.append(num & 0xFF)
    buffer.append(footer)
    buffer.append(footer)
    return buffer

# 时间控制参数
clock = time.clock()
last_laser_send = time.ticks_ms()  # 统一发送时间戳
send_red_next = True               # 交替发送标志
laser_interval = 10

while True:
    clock.tick()
    img = sensor.snapshot()
    current_time = time.ticks_ms()

    # UART协议解析状态机
    while uart.any():
        byte = uart.read(10)
        if byte:
            if byte[0] == 0xff and byte[-1] == 0xfe:
                if trigger_rect == 0:
                    trigger_rect = 1
                if trigger_rect == 2 and len(byte) >= 3 and 0 <= int(byte[1]) <= 3:
                    uart.write(pack_data(rect_coords[int(byte[1])], 0x01))


    # 矩形检测及发送
    if trigger_rect == 1:
        rects = img.find_rects(threshold=3500, roi=(40,30,200,150))
        if rects:
            for r in rects:
                if r.w() > 30 and r.h() > 30:
                    corners = r.corners()
                    points = list(corners)

                    cx = sum(p[0] for p in points) / 4
                    cy = sum(p[1] for p in points) / 4

                    def get_angle(p):
                        dx = p[0] - cx
                        dy = cy - p[1]
                        return math.atan2(dy, dx)

                    points = sorted(points, key=lambda p: get_angle(p), reverse=True)

                    for idx, (x, y) in enumerate(points):
                        rect_coords.append((x, y))
                        img.draw_circle(x, y, 3, color=(0,0,255))
                        label = "X{}".format(idx+1)
                        text_x = x + 5 if x < 280 else x - 30
                        text_y = y + 5 if y < 220 else y - 15
                        img.draw_string(text_x, text_y, label,
                                      color=(255,255,255),
                                      scale=1.2,
                                      mono_space=False,
                                      bg_color=(0,0,255))
                    img.draw_rectangle(r.rect(), color=(255,0,0), thickness=2)
                    trigger_rect = 2
                    break

    # 激光检测逻辑
    if trigger_rect == 0 or trigger_rect == 2:
        red_coords = None
        green_coords = None

        # 红色激光检测
        red_blobs = img.find_blobs([RED_LASER_THRESHOLD],
                                pixels_threshold=15,
                                area_threshold=15,
                                merge=True,
                                margin=5)
        if red_blobs:
            max_red = max(red_blobs, key=lambda b: (b.area(), -b.y()))
            red_coords = (max_red.cx(), max_red.cy())
            img.draw_circle(red_coords[0], red_coords[1], 8, color=(255,0,0))
            img.draw_string(red_coords[0]+10, red_coords[1]+10,
                          "R:({},{})".format(*red_coords),
                          color=(255,0,0), scale=1.5, bg_color=(0,0,0))

        # 绿色激光检测
        green_blobs = img.find_blobs([GREEN_LASER_THRESHOLD],
                                   pixels_threshold=15,
                                   area_threshold=15,
                                   merge=True,
                                   margin=5)
        if green_blobs:
            max_green = max(green_blobs, key=lambda b: (b.area(), -b.y()))
            green_coords = (max_green.cx(), max_green.cy())
            img.draw_circle(green_coords[0], green_coords[1], 8, color=(0,255,0))
            img.draw_string(green_coords[0]+10, green_coords[1]+10,
                          "G:({},{})".format(*green_coords),
                          color=(0,255,0), scale=1.5, bg_color=(0,0,0))

        # 交替发送逻辑（核心修改部分）
        if current_time - last_laser_send >= 200:
            if send_red_next:
                if red_coords:
                    uart.write(pack_data(red_coords, 0x02))
                    print("Red sent:", red_coords)
                    send_red_next = False
                    last_laser_send = current_time
                elif green_coords:  # 红色不存在时尝试发送绿色
                    uart.write(pack_data(green_coords, 0x03))
                    print("Green sent:", green_coords)
                    send_red_next = True
                    last_laser_send = current_time
            else:
                if green_coords:
                    uart.write(pack_data(green_coords, 0x03))
                    print("Green sent:", green_coords)
                    send_red_next = True
                    last_laser_send = current_time
                elif red_coords:  # 绿色不存在时尝试发送红色
                    uart.write(pack_data(red_coords, 0x02))
                    print("Red sent:", red_coords)
                    send_red_next = False
                    last_laser_send = current_time

    # 按键处理
    if KEY.is_press():
        trigger_rect = 1 if trigger_rect == 0 else 0

    lcd.display(img)
    lcd.draw_string(0, 0, "YIBAI4", lcd.RED, lcd.WHITE)
    lcd.draw_string(220, 0, "TR:{}".format(trigger_rect), lcd.RED, lcd.WHITE)

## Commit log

2025-04-01 4.2第一次上传
2025-04-01 4.2提交2
2025-04-03 增加了3d打印文件，整理了一下
    [scene.stl_1.3mf, 步进电机云台1234.3mf, 步进电机云台234.3mf]
2025-04-08 上传了第一版EDA硬件板子
2025-04-10 K210红色色块识别，坐标标记及与单片机通信代码初版
2025-04-14 stm32初始化工程，使用vscode需要手动修改配置的keil路径
2025-04-14 添加OLED驱动，更新gitignore
2025-04-15 添加了部分motor代码
2025-04-16 写好了基于调整arr改变速度的motor，但是这是不应的
2025-04-18 步进电机改为了按步数和距离移动，添加了tim1 为10ms中断
2025-04-18 准备写menu
2025-04-18 red laser recognition
2025-04-19 添加了joystick操纵杆的库
2025-04-19 激光点识别
2025-04-19 删除多余文件
    [scene.stl_1.3mf, 步进电机云台1234.3mf, 步进电机云台234.3mf]
2025-04-19 更新了配置文件，添加了按键和adc操纵杆
2025-04-19 k210按键记录顶点
2025-04-19 TIM1定时中断，遥感、电池ADC
2025-04-19 操纵杆控制云台
2025-04-19 更新了第二版PCB板
2025-04-19 实现了摇杆控制，但是发现原来步进脉冲的方案不行
2025-04-19 绿色激光笔识别代码
2025-04-19 PCB第三版上传，按艺艺建议改了两个引脚
2025-04-20 实现了灵敏的摇杆操控
2025-04-20 第三版板子修改一些丝印
2025-04-20 没做什么
2025-04-20 menu菜单ui写完了，而且比我以前规范一点！
2025-04-20 像素距离转换写到一半，周二再继续写
2025-04-20 添加K210支架工程图
    [k210固定板.SLDPRT, k210固定板.STL, k210底座.SLDPRT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]
2025-04-20 云台装配文件stl版本
    [步进电机云台234.3mf, 步进电机云台234.stl]
2025-04-21 写了更新了电机控制函数，通过更改set可以控制电机朝向运动了。但是没测
2025-04-22 史诗级大改动！现在的代码和变量超级无敌简洁规范优雅可拓展
2025-04-22 改进了del更新函数
2025-04-22 修改TIM3 Arr 1ms触发一次
2025-04-22 增加了绿光识别及顺时针识别四角坐标的K210识别代码
2025-04-23 完成了运动逻辑，理论上现在只要矫正过后直接改动set值就可以移动
2025-04-23 基本完成了架构建设，还差发送给k210和debug
2025-04-23 4.23修改新增
2025-04-24 菜单写完了
2025-04-24 主要代码应该都完成了，进入调试阶段
2025-04-24 实现了摇杆灵敏控制
2025-04-24 K210部分通信代码更新
2025-04-25 调试中途的版本，现在按下回原点的按键会真的回到原点，原因未知
2025-04-25 按一次不能回，按两次就能回，很奇怪的其他现象
2025-04-25 del初始被设定为了159.94，不知道是在哪
2025-04-26 解决了一些莫名其妙的问题，可以实现要求1和2的运动
2025-04-26 写好通信了
2025-04-26 没改什么
2025-04-26 4.26最新K210代码
2025-04-27 修复k210通信
2025-04-28 修复与k210的通信，现在可以正常传输当前激光坐标
2025-04-28 更新cubemx配置
2025-04-28 初步完成矩形坐标的传输
2025-05-01 发现会莫名其妙退出回原点模式，原因未知，添加了一些调试用代码
2025-05-01 完成要求一
2025-05-01 完成要求二，23
2025-05-01 给第二问矫正了一下
2025-05-01 更精细的矫正
2025-05-01 5.1日矩形框识别
2025-05-01 k210矩形识别标志位
2025-05-01 勉强完成要求三四，时常出线不够扣分
2025-05-03 现在使用计算来更新del值，抖动情况改善，但还是容易跑出线
2025-05-03 添加屏幕距离作为系统参数
2025-05-05 新增运动机的代码
2025-05-06 添加电机支撑件3d模型
    [电机支撑件.SLDPRT, 电机支撑件.STL]
2025-05-06 将红绿激光分开，绿色写了通信部分，绿色使用now计算del控制
2025-05-06 更新gitignore
2025-05-06 更新电机支撑件3d模型
    [电机支撑件.SLDPRT, 电机支撑件.STL]
2025-05-07 sy修改前的版本
    [步进电机云台1234.3mf]
2025-05-08 基本完成绿色激光控制
2025-05-09 完成绿色激光
2025-05-09 自定义行走模式完成！
2025-05-09 绿色8ms一步
2025-05-09 修复通信bug
2025-05-09 初审作品！
2025-05-10 （未测试）让绿色的蜂鸣器只在有识别到红色激光的时候才响
2025-05-10 新增运动机自调整与K230端的代码
2025-05-11 自定义路径队列不清空
2025-05-11 绿色调快一点
2025-05-28 制作了主控板pcbv4
2025-05-28 添加了转接板
2025-05-28 修改后板子

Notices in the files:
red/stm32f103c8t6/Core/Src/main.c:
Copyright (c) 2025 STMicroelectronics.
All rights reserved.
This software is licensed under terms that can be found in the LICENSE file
